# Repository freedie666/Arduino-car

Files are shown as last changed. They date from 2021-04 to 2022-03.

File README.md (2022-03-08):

# Arduino Car
  
Robotic car that follows line drawn on the ground using arduino.

Project was created at BUT-FIT
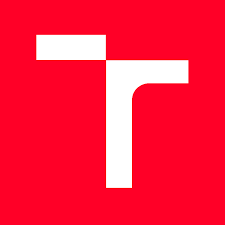
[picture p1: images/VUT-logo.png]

, class IMR.

<p align="center">
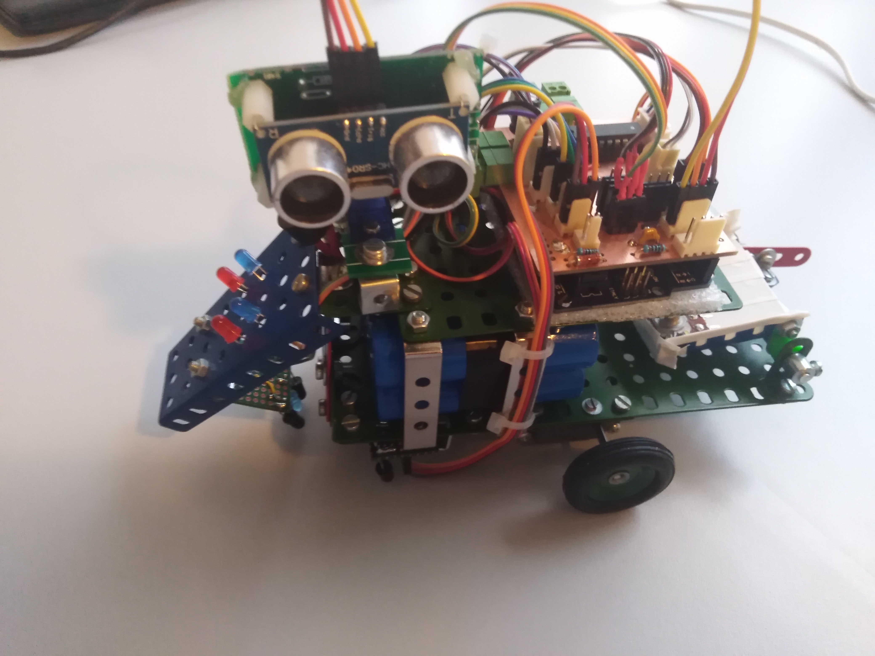
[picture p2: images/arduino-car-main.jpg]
  
</p>

## What robot does

> - Follows line at the ground
> - Can detect extra line that tells robot where to go at the crossroads
> - Extra lines can give robot additional orders
> - Detection of obstacle on the line
> - Robot can find best way around obstacle and avoid it
> - Is able to carry cargo and unload it on command
> - Sings a song when detects obstacle
> - Has multiple Blue and RED LEDs that show its intentions
> - Carries its own power source - batteries

## How its done

> - Brain of the operation is Arduino UNO
> - Car is powered by two 12V DC motors with gearbox
> - Motors are controlled by motor driver LV8406 using PWM
> - Lines are detected by infrared emiting LED and phototransistor [3x LED and 4x phototransistors]
> - Speed and directions are controlled by P-regulator
> - Obstacles are detected with ultrasonic sensor HC-SR04 
> - Ultrasonic sensor is mounted on small servo, providing range of detection up to +-90° 
> - Cargo beds movement is provided by stepper motor 2BYJ-48
> - Blue and RED LEDs are controlled by WS2818B led driver
> - Buzzer can play All star song which is stored in Flash memory

## Last notes

> - Everything electical is soldered at custom made PCB which fits onto Arduino as Arduino shield
> - Song is stacked in memory in a way to save as much memory as possible [4 numbers in one unsigned short]
  
## Links 
Demonstration of car at [Youtube](https://www.youtube.com/watch?v=gtERXzQzxGM)

More photos and videos at [Google Drive](https://drive.google.com/drive/folders/1pzaO6EnN3uHb_-Xj_Ckr5q-n50d8h_We?usp=sharing)

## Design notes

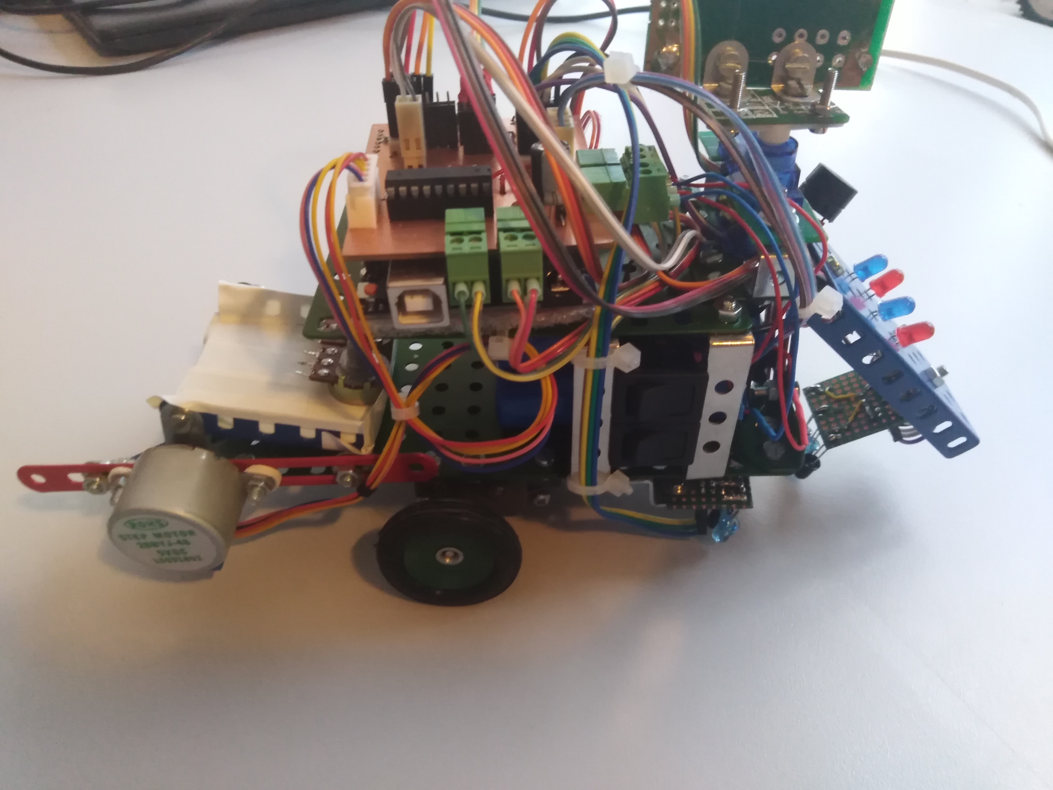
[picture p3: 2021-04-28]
images/arduino-car-main2.jpg

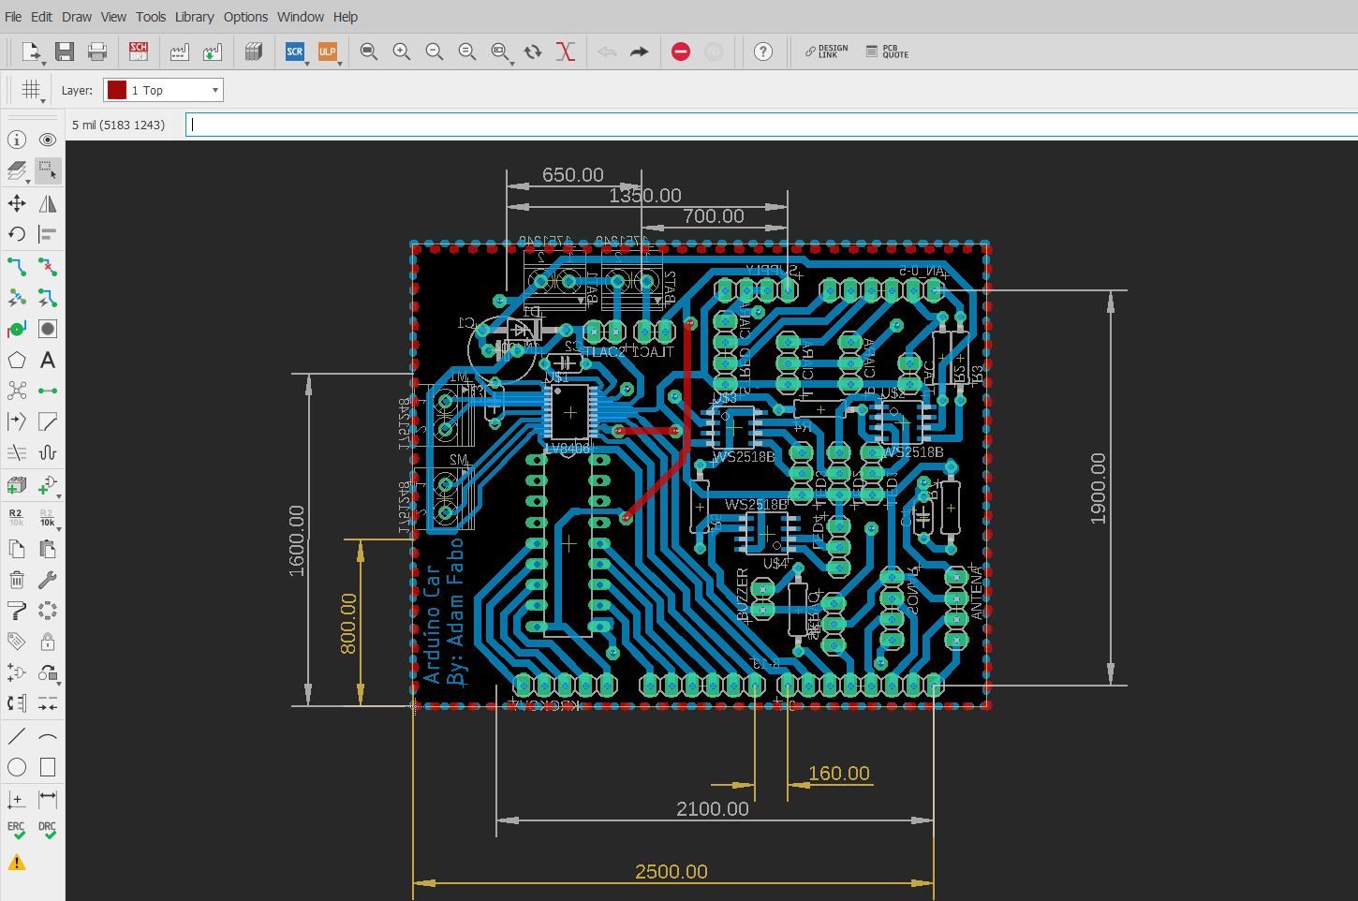
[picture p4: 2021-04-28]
PCB/PCB1.png

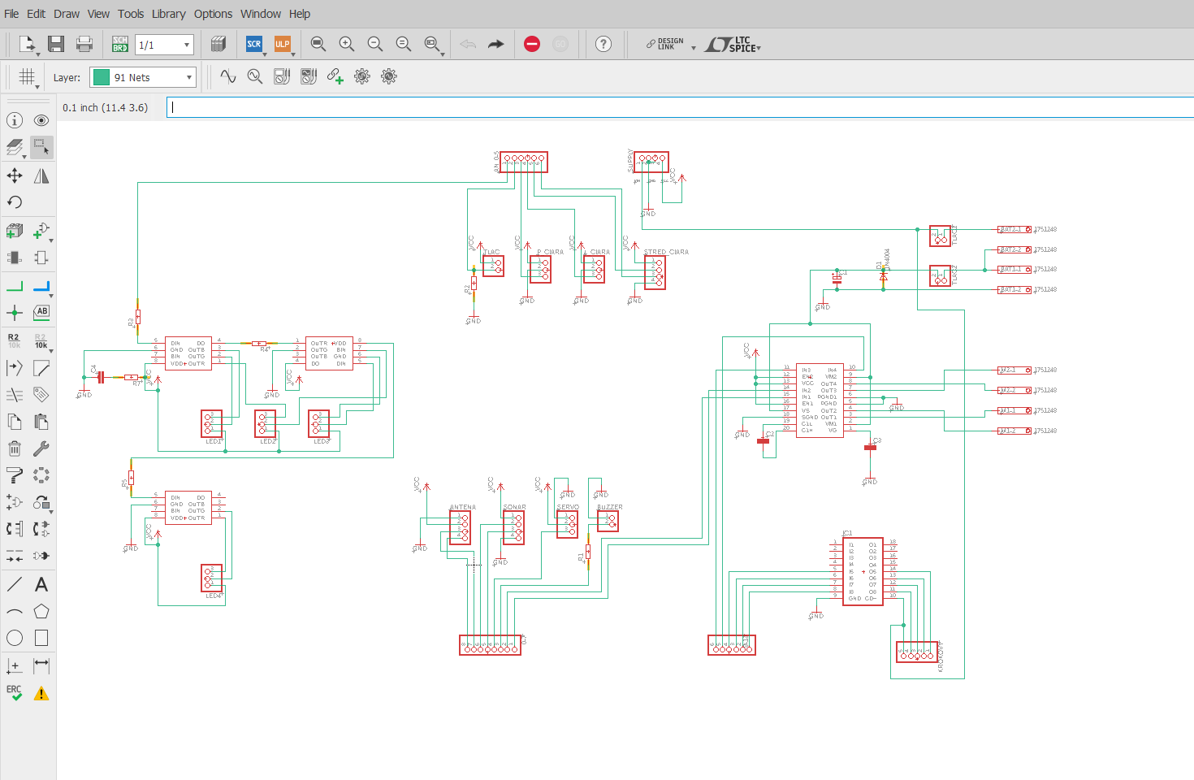
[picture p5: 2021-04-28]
PCB/PCB2.png

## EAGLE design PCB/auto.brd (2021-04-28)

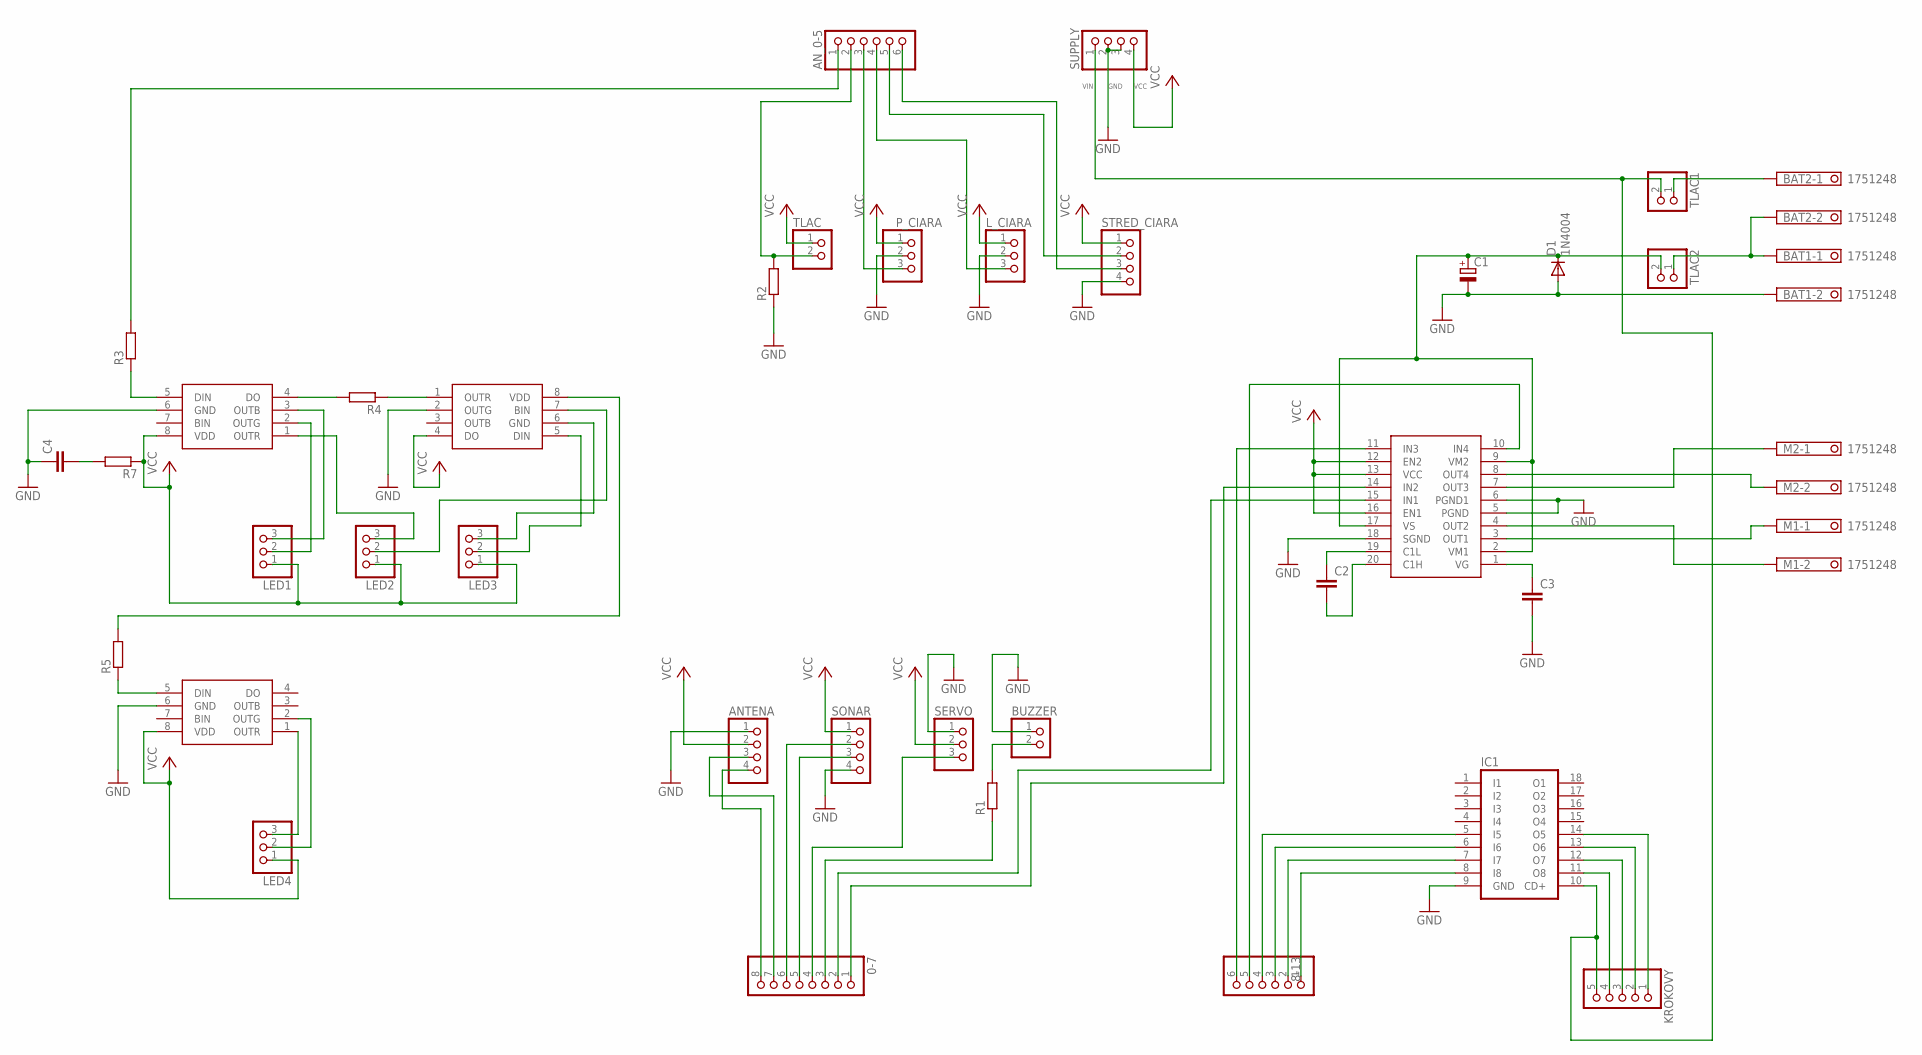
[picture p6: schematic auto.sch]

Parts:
0-7: PINHD-1X8; 1X08
8-13: PINHD-1X6; 1X06
ANTENA: PINHD-1X4; 1X04
AN_0-5: PINHD-1X6; 1X06
BAT1, BAT2: 1751248
BUZZER: PINHD-1X2; 1X02
C1: CPOL-EUE3.5-8; E3,5-8
C2, C3, C4: C-EU050-024X044; C050-024X044
D1: 1N4004; DO41-10
IC1: ULN2804A; DIL18
KROKOVY: PINHD-1X5; 1X05
LED1, LED2, LED3, LED4: PINHD-1X3; 1X03
L_CIARA: PINHD-1X3; 1X03
M1, M2: 1751248
P_CIARA: PINHD-1X3; 1X03
R1, R2, R3, R4, R5, R7: R0207/10; 0207/10
SERVO: PINHD-1X3; 1X03
SONAR: PINHD-1X4; 1X04
STRED_CIARA: PINHD-1X4; 1X04
SUPPLY: PINHD-1X4; 1X04
TLAC, TLAC1, TLAC2: PINHD-1X2; 1X02
U$1: LV8406; TSSOP20
U$2, U$3, U$4: WS2518B; SOP08

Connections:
GND: ANTENA.1, BAT1.2, BUZZER.1, C1.-, C3.2, C4.1, D1.A, IC1.9 (GND), L_CIARA.2, P_CIARA.2, R2.1, SERVO.1, SONAR.4, STRED_CIARA.4, SUPPLY.2, SUPPLY.3, U$1.5 (PGND), U$1.6 (PGND1), U$1.18 (SGND), U$2.6 (GND), U$3.2 (OUTG), U$4.6 (GND)
unnamed: AN_0-5.6, STRED_CIARA.3
unnamed: AN_0-5.5, STRED_CIARA.2
unnamed: AN_0-5.4, L_CIARA.3
unnamed: AN_0-5.3, P_CIARA.3
unnamed: 0-7.6, SONAR.2
unnamed: 0-7.5, SONAR.3
unnamed: 0-7.4, SERVO.3
unnamed: C3.1, U$1.1 (VG)
unnamed: BAT1.1, BAT2.2, TLAC2.1
unnamed: BUZZER.2, R1.2
unnamed: 0-7.3, R1.1
unnamed: BAT2.1, TLAC1.1
unnamed: 8-13.4, IC1.5 (I5)
unnamed: 8-13.3, IC1.6 (I6)
unnamed: 8-13.2, IC1.7 (I7)
unnamed: 8-13.1, IC1.8 (I8)
unnamed: M1.1, U$1.3 (OUT1)
unnamed: IC1.11 (O8), KROKOVY.4
unnamed: IC1.12 (O7), KROKOVY.3
unnamed: IC1.14 (O5), KROKOVY.1
unnamed: IC1.13 (O6), KROKOVY.2
unnamed: M1.2, U$1.4 (OUT2)
unnamed: M2.1, U$1.7 (OUT3)
unnamed: M2.2, U$1.8 (OUT4)
unnamed: C1.+, D1.C, TLAC2.2, U$1.2 (VM1), U$1.9 (VM2), U$1.17 (VS)
unnamed: 8-13.5, U$1.10 (IN4)
unnamed: 8-13.6, U$1.11 (IN3)
unnamed: C2.1, U$1.19 (C1L)
unnamed: C2.2, U$1.20 (C1H)
unnamed: R5.1, U$4.5 (DIN)
unnamed: LED4.3, U$4.1 (OUTR)
unnamed: 0-7.1, U$1.14 (IN2)
unnamed: R5.2, U$3.8 (VDD)
unnamed: AN_0-5.1, R3.2
unnamed: LED2.2, U$3.7 (BIN)
unnamed: LED1.3, U$2.3 (OUTB)
unnamed: LED4.2, U$4.2 (OUTG)
unnamed: R4.1, U$3.1 (OUTR)
unnamed: R3.1, U$2.5 (DIN)
unnamed: LED3.3, U$3.6 (GND)
unnamed: LED3.2, U$3.5 (DIN)
unnamed: AN_0-5.2, R2.2, TLAC.2
unnamed: 0-7.2, U$1.15 (IN1)
unnamed: LED1.2, U$2.2 (OUTG)
unnamed: 0-7.7, ANTENA.3
unnamed: 0-7.8, ANTENA.4
unnamed: R4.2, U$2.4 (DO)
unnamed: LED2.3, U$2.1 (OUTR)
unnamed: C4.2, R7.2
VCC: ANTENA.2, LED1.1, LED2.1, LED3.1, LED4.1, L_CIARA.1, P_CIARA.1, R7.1, SERVO.2, SONAR.1, STRED_CIARA.1, SUPPLY.4, TLAC.1, U$1.12 (EN2), U$1.13 (VCC), U$1.16 (EN1), U$2.8 (VDD), U$3.4 (DO), U$4.8 (VDD)
VIN: IC1.10 (CD+), KROKOVY.5, SUPPLY.1, TLAC1.2

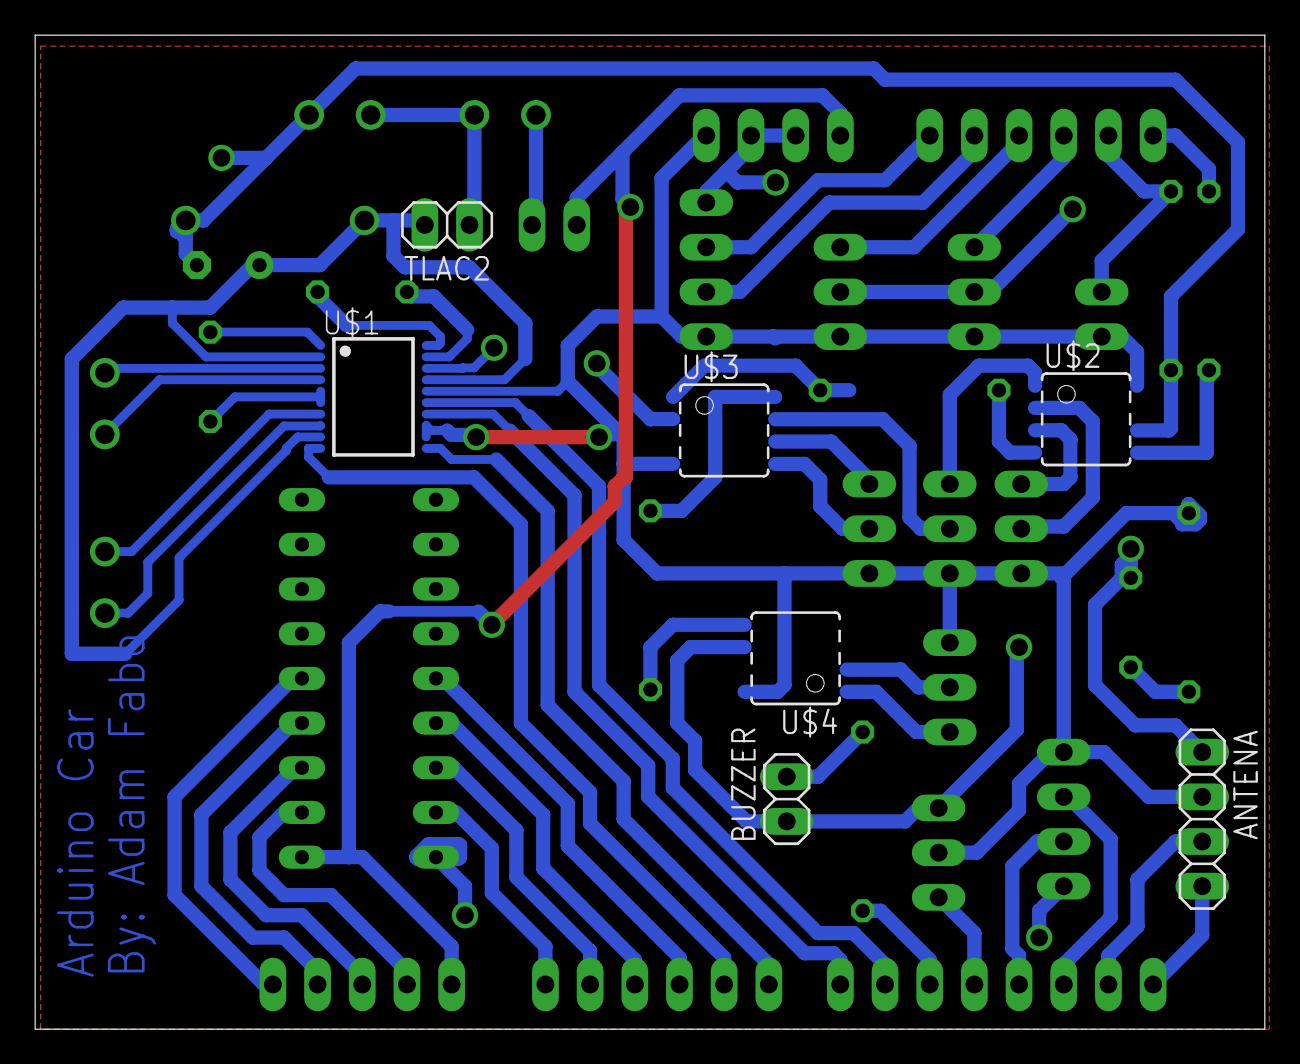
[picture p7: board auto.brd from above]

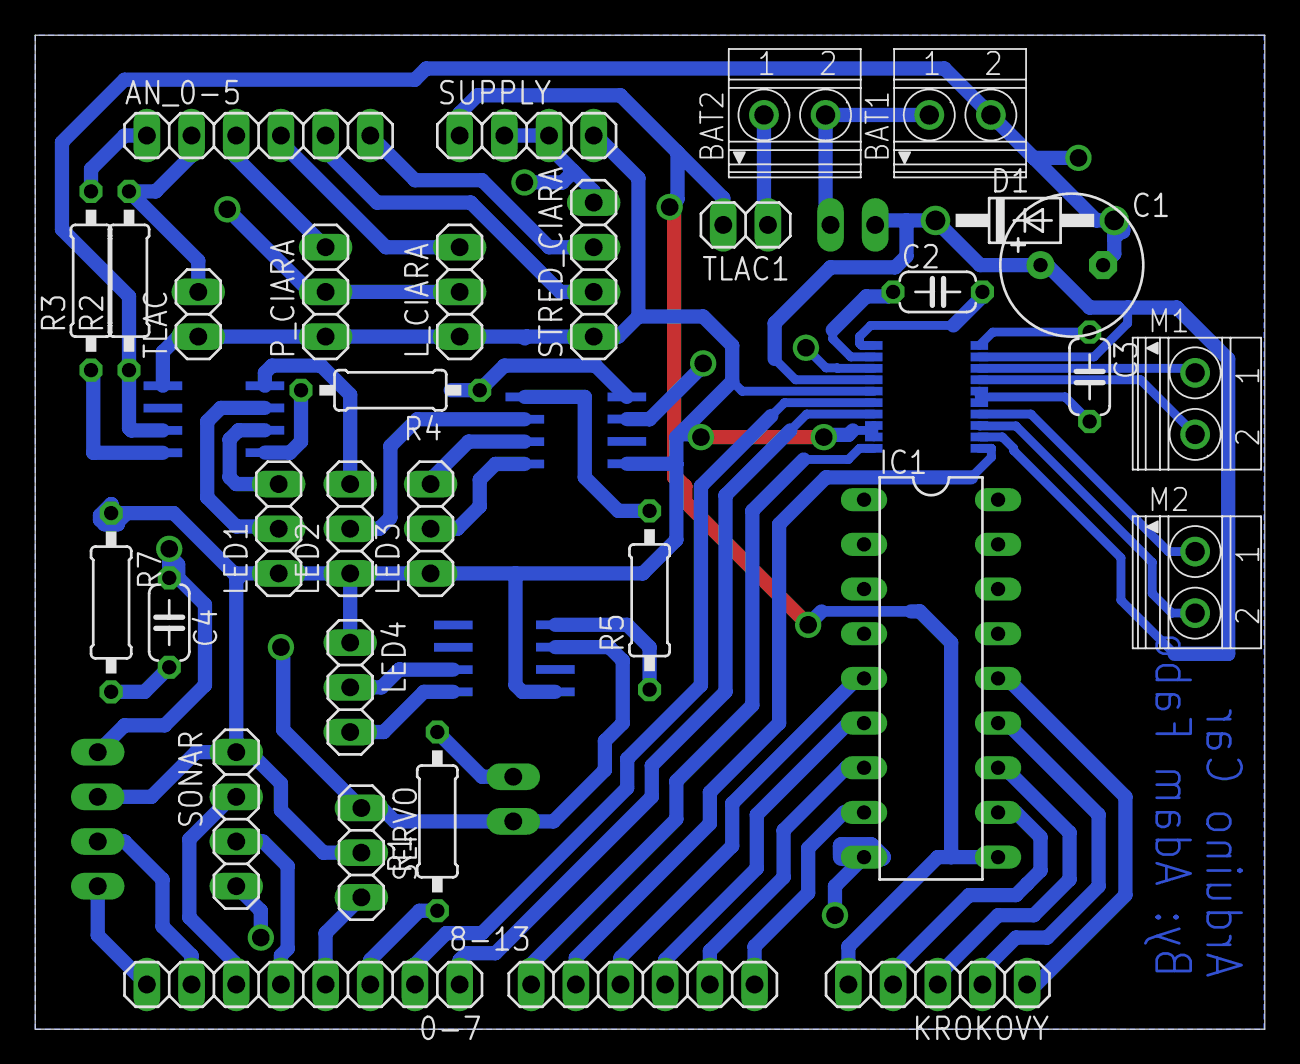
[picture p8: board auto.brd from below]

Board: 2 copper layers, 69.9 x 56.5 mm, 39 parts (32 on the bottom side), 52 nets.

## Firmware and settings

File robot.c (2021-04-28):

// Proejkt na predmet IMR
// Autor: Adam Fabo
// Subor obsahuje kod pre ovladanie pohybu robota po ciernej ciare 

#include <Servo.h>
// 3 lavy

// data pre all-star melodiu
const short PROGMEM tones[]   =  {370, 554, 466, 466, 415, 370, 370, 494, 466, 466, 415, 415, 370, 370, 554, 466, 466, 415, 370, 370, 311, 277, 370, 370, 554, 466, 466, 415, 415, 369, 369, 494, 466, 466, 415, 415, 369, 369, 554, 466, 466, 415, 369, 369, 415, 311, 369, 311, 369, 369, 369, 369, 311, 277, 369, 369, 369, 369, 369, 369, 369, 369, 369, 369, 369, 369, 369, 466, 369, 466, 466, 554, 494, 466, 369, 415, 415, 415, 415, 466, 369, 369, 311, 277, 369, 369, 369, 466, 554, 466, 622, 466, 554, 466, 622, 466, 554, 494, 466, 415, 369, 369, 415, 369, 369, 369, 369, 369, 369, 369, 369, 369, 369, 369, 466, 369, 369, 369, 311, 311};
const unsigned short dels[] PROGMEM  = {16932, 16930, 8738, 8740, 8740, 8804, 8738, 16930, 8738, 9250, 8770, 4964, 4386, 8721, 4625, 4385, 4625, 8467, 8466, 8498, 4386, 4642, 4626, 4626, 8738, 16914, 8465, 16913, 4369, 8466};

Servo myservo;

// sonar
#define ECHO_PIN 3
#define TRIG_PIN 2

//buzzer
#define PIEZO_PIN 4
#define TONES_LEN 120

//servo
#define SERVO_PIN 5

//motor
#define MOTOR_L1 6
#define MOTOR_L2 7
#define MOTOR_R1 8
#define MOTOR_R2 9

//krokovy motor
#define STEPPER_1 10
#define STEPPER_2 11
#define STEPPER_3 12
#define STEPPER_4 13

//pocet krokov potrebnych na zodvihnutie korby
#define STEPPER_STEPS 150

//led driver
#define LED_PIN 19

// flagy pre nastavovanie lediek
#define NONE  B00000000
#define RBLUE B00000001
#define LBLUE B00000010
#define LRED  B00000100
#define RRED  B00001000



#define DIST_target 15.0
#define DIST_target_wall 22.0
#define DIST_koef_add 9
#define DIST_koef_sub 3


#define target  700       // Koeficienty P regulatora pre snimanie stredu ciary
#define P_koef_add  0.7
#define P_koef_sub  1.5


#define target_low 200   // Koeficienty P regulatora pre snimanie hrany ciary
#define target_high 700
#define P_koef_add_hrana  0.2
#define P_koef_sub_hrana  0.5

#define hysteresis_up 650
#define hysteresis_down 450

#define koef 2

unsigned int min_speed     = 300 * koef;    // toto teoreticky cez define
unsigned int max_speed_add = 40  * koef;
unsigned int max_speed_sub = 20  * koef;

unsigned int periode = 1000 * koef;         // toto teoreticky cez define

unsigned int avgR = 500;
unsigned int avgL = 500;

unsigned long int smerovka_vpravo = 0;
unsigned long int smerovka_vlavo  = 0;

enum Mode { MODE_STRAIGHT, MODE_LEFT, MODE_RIGHT, MODE_GIVEN_RIGHT, MODE_GIVEN_LEFT,  MODE_KORBA};
Mode mode = MODE_STRAIGHT;
Mode mode_old = -1;// na zaciatok nejaku nevalidnu hodnotu

Mode modes_arr[] = {MODE_GIVEN_LEFT,MODE_KORBA};
int modes_counter = 0;

unsigned int filter_up = 18;              // toto teoreticky cez define
unsigned int filter_down = 40;            // toto teoreticky cez define


unsigned int counter = 6;                 // toto teoreticky cez define

unsigned int cnt = 0;

long duration;
float distance;

unsigned int delR = min_speed;
unsigned int delL = min_speed;

unsigned int num_of_cycles = 250;

unsigned int range_slow = 0;
bool once  = true;


unsigned int not_ciara_koef = 50 * koef;


int x = 20000;
bool can_go = true;
int pos = 0;
#define treshold  800;



void setup() {
  pinMode(TRIG_PIN, OUTPUT);     // sonar
  pinMode(ECHO_PIN, INPUT);

  pinMode(PIEZO_PIN, OUTPUT);

  pinMode(MOTOR_L1, OUTPUT);    // motor
  pinMode(MOTOR_L2, OUTPUT);
  pinMode(MOTOR_R1, OUTPUT);
  pinMode(MOTOR_R2, OUTPUT);

  pinMode(STEPPER_1, OUTPUT);   // krokovy
  pinMode(STEPPER_2, OUTPUT);
  pinMode(STEPPER_3, OUTPUT);
  pinMode(STEPPER_4, OUTPUT);

  digitalWrite(STEPPER_1, LOW);
  digitalWrite(STEPPER_2, LOW);
  digitalWrite(STEPPER_3, LOW);
  digitalWrite(STEPPER_4, LOW);

  myservo.attach(SERVO_PIN);
  Serial.begin(230400);
  Serial.println("Lets start this bitch");

  pinMode(LED_PIN, OUTPUT);
  digitalWrite(LED_PIN, LOW);
}


// hlavna smycka programu
void loop() {

  // stara sa o detekciu prekazok, ak na nejaku narazi tak prebera vedenie robota a postara sa o obidenie prekazky
  // ak ziadnu prekazku nedetekoval tak konci
  // ak detekoval potencialnu prekazku tak nastavuje hodnotu range_slow ktora spomali auto az dokedy bud nedetekuje prekazku uplne
  // alebo prekazka zmizne
  // taktiez nastavuje aj num_of_cycles - cim blizsie ku prekazke, tym menej cyklov
  obstacle_detection();


  main_func();

}

// hlavna funkcia robota
void main_func() {

  for (unsigned i = 0; i < num_of_cycles; i++) {
    // nastavenie serva dopredu
    myservo.write(80);

    // spomalenie robota ak je blizko prekazky
    delR -= min(range_slow, delR);
    delL -= min(range_slow, delL);

    motor_forward_PWM();



    // hodoty hlavneho snimaca ciary
    avgR = analogRead(1);
    avgL = analogRead(0);


    // branie kazdej n-tej hodnoty na spomalenie rastu hodnoti s kombinacou filtra
    // ak napr auto krizuje inu ciaru tak aby to nebralo ako falosnu detekciu smerovacej ciary
    if (i % counter == 0) {
      smerovka_vpravo = (filter_down * smerovka_vpravo + analogRead(2)) / (filter_down + 1) ;
      smerovka_vlavo  = (filter_down * smerovka_vlavo  + analogRead(3)) / (filter_down + 1) ;
    }

    /*Serial.print("\t");

      Serial.print(" smerovka_vpravo:  ");
      Serial.print(smerovka_vpravo);
      Serial.print("\t");
      Serial.print(" smerovka_vlavo:  ");
      Serial.println(smerovka_vlavo);*/


    if (mode == MODE_RIGHT || mode == MODE_GIVEN_RIGHT) {

      // Drzanie sa pravej hrany pasky

      if (mode != mode_old ) {
        Serial.println("MODE_RIGHT");
        Serial.println(mode);
        mode_old = mode;
        if (mode == MODE_RIGHT)
          shine_LED(RRED);
        else
          shine_LED(RBLUE | RRED);
      }


      //cast hysterezy
      if (mode == MODE_RIGHT && smerovka_vpravo < hysteresis_down ) {
        mode = MODE_STRAIGHT;
      } else if (mode == MODE_GIVEN_RIGHT && smerovka_vpravo < hysteresis_down && smerovka_vlavo < hysteresis_down) {
        mode = MODE_STRAIGHT;
      }

      calc_speed_right();

    } else if (mode == MODE_LEFT || mode == MODE_GIVEN_LEFT) {

      // Drzanie sa lavej hrany pasky

      if (mode != mode_old ) {
        Serial.println("MODE_LEFT");
        Serial.println(mode);
        mode_old = mode;
        if (mode == MODE_LEFT) {
          shine_LED( LRED);
        } else {
          shine_LED(LBLUE | LRED);
        }

      }
      //Serial.print("Dolava ");

      //cast hysterezy
      if (mode == MODE_LEFT && smerovka_vlavo < hysteresis_down ) {
        mode = MODE_STRAIGHT;
      } else if (mode == MODE_GIVEN_LEFT && smerovka_vpravo < hysteresis_down && smerovka_vlavo < hysteresis_down) {
        mode = MODE_STRAIGHT;
      }

      calc_speed_left();



    } else if (mode == MODE_STRAIGHT) {

      if (mode != mode_old ) {
        Serial.println("MODE_STRAIGHT");
        Serial.println(mode);
        mode_old = mode;
        shine_LED(LBLUE | RBLUE);
      }

      //Serial.print("No smer ");

      if (smerovka_vpravo > hysteresis_up && smerovka_vlavo < hysteresis_down) {
        mode  = MODE_RIGHT;

      } else if (smerovka_vlavo > hysteresis_up && smerovka_vpravo < hysteresis_down) {
        mode = MODE_LEFT;

      } else if (smerovka_vpravo > hysteresis_up && smerovka_vlavo > hysteresis_down) {

        mode = modes_arr[modes_counter % 2];
        modes_counter++;
        if(mode == MODE_KORBA){
          stepper_seq();
          mode = MODE_GIVEN_LEFT;
        }
          
      }

      calc_speed_straight();
    }

    delR = min(delR, periode);
    delL = min(delL, periode);
    Serial.print("  ");
    Serial.print(range_slow);
    Serial.print("  ");


    if (delR > delL) {
      Serial.print(" dolava \t");
    } else if (delR < delL) {
      Serial.print(" doprava \t");
    } else {
      Serial.print(" rovno \t");
    }

    Serial.print("\t");
    Serial.print(avgR);
    Serial.print(" R");
    Serial.print("\t");
    Serial.print(avgL);
    Serial.print(" L");


    Serial.print("\t");
    Serial.print(delR);
    Serial.print(" delR");
    Serial.print("\t");
    Serial.print(delL);
    Serial.println(" delL");


  }
}





void calc_speed_right() {
  if (avgL >= target_high && avgR <= target_low) { //chod rovno
    delR = min_speed;
    delL = min_speed;

  } else if (avgL <= target_high && avgL >= target_low && avgR <= target_low) { //ak je mimo kraja, viacej vlavo
    delL = min_speed - min(P_koef_sub_hrana * (target_high - avgL), min_speed);
    delR = min_speed + P_koef_add_hrana * (target_high - avgL);

  } else if (avgL >= target_high && avgR >= target_low) {                       //ak je trosku mimo stredu, viacej vpravo
    delL = min_speed + P_koef_add_hrana * (avgR - target_low);
    delR = min_speed - min(P_koef_sub_hrana * (avgR - target_low), min_speed);

  } else if (avgL <= target_low && avgR <= target_low) {    //ak je mimo ciary pokracuj v predoslom smere
    ;
    //delR = 0;
    //delL = 0;
  }
}


void calc_speed_left() {

  if (avgR >= target_high  &&  avgL <= target_low) { //chod rovno
    delR = min_speed;
    delL = min_speed;

  } else if (avgR <= target_high && avgR >= target_low && avgL <= target_low) { //ak je mimo kraja, viacej vlavo
    delR = min_speed - min(P_koef_sub_hrana * (target_high - avgR), min_speed);
    delL = min_speed + P_koef_add_hrana * (target_high - avgR);

  } else if (avgR >= target_high && avgL >= target_low) {                     //ak je trosku mimo stredu, viacej vpravo
    delR = min_speed + P_koef_add_hrana * (avgL - target_low);
    delL = min_speed - min(P_koef_sub_hrana * (avgL - target_low), min_speed);


  } else if (avgL <= target_low && avgR <= target_low) {                    //ak je mimo ciary pokracuj v predoslom smere
    ;//delR = 0;
    Serial.print(" POKRACUJEM  ");
    //delL = 0;
  }
}

void calc_speed_straight() {
  if (avgR >= target && avgL >= target) {                               //chod rovno
    delR = min_speed;
    delL = min_speed;

  } else if (avgR >= target && avgL < target) {                            //ak je to trosku mimo stredu, viacej vlavo
    delR = min_speed - min(P_koef_sub * (target - avgL), min_speed);
    delL = min_speed + P_koef_add * (target - avgL);

  } else if (avgR < target && avgL >= target) {                           //ak je to trosku mimo stredu, viacej vpravo
    delR = min_speed + P_koef_add * (target - avgR);
    delL = min_speed -  min(P_koef_sub * (target - avgR), min_speed);

  } else if (avgR < target && avgL < target && avgR < 100 && avgL < 100) { //ak su obe mimo pokracuj v smere kam si siel
    ;//delR = 0;
    Serial.print(" POKRACUJEM  ");
    // delL = 0;

  } else if (avgR < target && avgL < target && avgR > avgL) {             //ak je to mimo vlavo
    delR = min_speed - min(P_koef_sub * (target - avgL), min_speed); //0
    delL = min_speed + P_koef_add * (target - avgL);

  } else if (avgR < target && avgL < target && avgR < avgL) {            //ak je to mimo vpravo
    delR = min_speed + P_koef_add * (target - avgR);
    delL = min_speed - min(P_koef_sub * (target - avgR), min_speed); //0
  }
}

// stara sa o detekciu prekazok, ak na nejaku narazi tak prebera vedenie robota a postara sa o obidenie prekazky
// ak ziadnu prekazku nedetekoval tak konci
// ak detekoval potencialnu prekazku tak nastavuje hodnotu range_slow ktora spomali auto az dokedy bud nedetekuje prekazku uplne
// alebo prekazka zmizne
// taktiez nastavuje aj num_of_cycles - cim blizsie ku prekazke, tym menej cyklov
void obstacle_detection() {


  sonar();

  if (distance > DIST_target &&  distance < DIST_target + 15) {
    // ak este nenarazil na prekazku ale prekazka je uz blizko

    num_of_cycles = max(250 - (DIST_target - distance) * 10, 100);
    range_slow    = min((DIST_target + 15 - distance  ) * 9, 80);
    

    Serial.print(num_of_cycles );
    Serial.print(" " );
    Serial.print(range_slow );
    Serial.print(" " );
    Serial.print(distance);
    Serial.println(" cm");


  } else if (distance < DIST_target) {
    //ak uz narazil na prekazku

    delR = 0;
    delL = 0;

    stop_motor();

    obstacle_seq();
    range_slow = 0;
    return;

  } else {
    num_of_cycles = 500 ;
    range_slow    = 0;
  }
}

// sekvencia ktora sa vykona ak robot natrafi na prekazku
void obstacle_seq() {
  // na zaciatku nejake zapiskanie
  //sing_a_song();
  delay(5000);

  // nasnimanie vzdialenosti
  int dst = 15;
  for (int i = 0; i < 10; i++) {
    sonar();

    //vyfiltrovanie vzdialenosti
    dst = (9 * dst + distance) / (9 + 1);
  }

  //ak tam uz prekazka nie je tak ide sa dalej
  if (dst > 15)
    return;

  //zistenie ci nahodou robot nestoju na pomocnych pasikoch ktore by udavali jeho nasledovny smer
  for (int i = 0 ; i < 20; i++) {
    //filter na spomalenie rastu hodnoty
    smerovka_vpravo = (9 * smerovka_vpravo + analogRead(2)) / (9 + 1) ;
    smerovka_vlavo  = (9 * smerovka_vlavo +  analogRead(3)) / (9 + 1) ;


    /*Serial.print("\t");
      Serial.print(smerovka_vpravo);
      Serial.print(" R");
      Serial.print("\t");
      Serial.print(smerovka_vlavo);
      Serial.println(" L");*/
  }

  int dstR = 0;
  int dstL = 0;


  if (smerovka_vlavo < 500 &&  smerovka_vpravo < 500) {
    // ak sa ani jeden pasik nenachadza tak sa robot rozhodne sam
    // podla toho na ktorej strane je vacsia volna vzdialenost tak tam pojde

    myservo.write(0);
    delay(1000);

    // ziskanie vzdialenosti doprava od robota
    for (int i = 0; i < 30; i++) {
      sonar();
      dstR = (9 * dstR + distance) / (9 + 1);
    }

    myservo.write(180);
    delay(1000);

    // ziskanie vzdialenosti dolava od robota
    for (int i = 0; i < 30; i++) {
      sonar();
      dstL = (9 * dstL + distance) / (9 + 1);
    }

    if (dstR < dstL) {
      rotate_left();

      myservo.write(0);
      delay(500);

      follow_right();

    } else {
      rotate_right();

      myservo.write(180);
      delay(500);

      follow_left();
    }


  } else if (smerovka_vlavo > 700 &&  smerovka_vpravo < 500) {
    // ak pomocny pasik je nalavo od robota

    rotate_left();

    myservo.write(0);
    delay(500);

    follow_right();

  } else if (smerovka_vlavo < 500 &&  smerovka_vpravo > 700) {
    // ak pomocny pasik je napravo od robota

    rotate_right();

    myservo.write(180);
    delay(500);

    follow_left();

  } else if ( (smerovka_vlavo > 500 &&  smerovka_vpravo > 700) || (smerovka_vlavo > 700 &&  smerovka_vpravo > 500) ) {
    ; // podla pamate

    rotate_right();

    myservo.write(180);
    delay(500);

    follow_left();
    
  }

}

// robot sa bude drzat steny co je nalavo od neho
void follow_left() {
  avgR = 0;
  avgL = 0;

  while (1) {
    myservo.write(170); // nastavenie serva dolava
    sonar();

    // orezanie maximalnej hodnoty ktoru moze sonar nasnimat
    // bez toho vdaka napr chybnej vzdialenosti alebo velkej hodnote by mohol robot zabludit
    distance = min(distance, 30);

    // P regulator na udrzanie si vzdialenosti od steny
    if (distance < DIST_target_wall) {
      delR = min_speed - min(DIST_koef_add * (abs(distance - DIST_target_wall)) + not_ciara_koef, min_speed);
      delL = min_speed + min(DIST_koef_sub * (abs(distance - DIST_target_wall)) + not_ciara_koef, min_speed);

    } else {
      delR = min_speed + min(DIST_koef_sub * (abs(distance - DIST_target_wall)) + not_ciara_koef, min_speed);
      delL = min_speed - min(DIST_koef_add * (abs(distance - DIST_target_wall)) + not_ciara_koef, min_speed);

    }

    for (int i = 0; i < 25; i++) {
      // snimanie honot z hlavneho snimaca,
      // na hodnoty je pouzity filter na spomalenie rastu hodnoty
      avgR = (9 * avgR + analogRead(1)) / (9 + 1) ;
      avgL = (9 * avgL + analogRead(0)) / (9 + 1) ;

      // ak narazil na ciaru tak sa nastavi zatocenie doprava a funkcia sa konci
      if (avgR > 700 || avgL > 700) {
        delR = 0;
        delL = 750;

        for (int j = 0; j < 100; j++) {
          Serial.println(" tuna sooooooooooooom");
          motor_forward_PWM();
        }

        return;
      }

      motor_forward_PWM();
    }
  }
}


// robot sa bude drzat steny co je napravo od neho
void follow_right() {
  avgR = 0;
  avgL = 0;

  while (1) {
    myservo.write(0);   // nastavenie serva doprava
    sonar();

    // orezanie maximalnej hodnoty ktoru moze sonar nasnimat
    // bez toho vdaka napr chybnej vzdialenosti alebo velkej hodnote by mohol robot zabludit
    distance = min(distance, 30);

    // P regulator na udrzanie si vzdialenosti od steny
    if (distance < DIST_target_wall) {
      delR = min_speed + min(DIST_koef_add * (abs(distance - DIST_target_wall)) + not_ciara_koef, min_speed);
      delL = min_speed - min(DIST_koef_sub * (abs(distance - DIST_target_wall)) + not_ciara_koef, min_speed);

    } else {
      delR = min_speed - min(DIST_koef_sub * (abs(distance - DIST_target_wall)) + not_ciara_koef, min_speed);
      delL = min_speed + min(DIST_koef_add * (abs(distance - DIST_target_wall)) + not_ciara_koef, min_speed);

    }

    for (int i = 0; i < 25; i++) {
      // snimanie honot z hlavneho snimaca,
      // na hodnoty je pouzity filter na spomalenie rastu hodnoty
      avgR = (9 * avgR + analogRead(1)) / (9 + 1) ;
      avgL = (9 * avgL + analogRead(0)) / (9 + 1) ;

      // ak narazil na ciaru tak sa nastavi zatocenie doprava a funkcia sa konci
      if (avgR > 700 || avgL > 700) {
        delR = 750;
        delL = 0;

        for (int j = 0; j < 100; j++)
          motor_forward_PWM();

        return;
      }

      motor_forward_PWM();
    }
  }
}

// otoci robota dolaba o zhruba 90 deg
// funkcia nema ziadnu spatnu vazbu takze zalezi iba od poctu cyklov
void rotate_left() {

  for (int i = 0; i < 550; i++) {

    digitalWrite(MOTOR_L1, HIGH);
    digitalWrite(MOTOR_R2, HIGH);


    digitalWrite(MOTOR_R1, LOW);
    digitalWrite(MOTOR_L2, LOW);

    int rotation_speed = 300 * koef;

    delayMicroseconds (rotation_speed);

    digitalWrite(MOTOR_R2, LOW);
    digitalWrite(MOTOR_L1, LOW);
    delayMicroseconds(periode - rotation_speed);
  }

  stop_motor();
}


// otoci robota doprava o zhruba 90 deg
// funkcia nema ziadnu spatnu vazbu takze zalezi iba od poctu cyklov
void rotate_right() {

  for (int i = 0; i < 550; i++) {
    digitalWrite(MOTOR_L1, LOW);
    digitalWrite(MOTOR_R2, LOW);


    digitalWrite(MOTOR_R1, HIGH);
    digitalWrite(MOTOR_L2, HIGH);

    int rotation_speed = 300 * koef;

    delayMicroseconds (rotation_speed);

    digitalWrite(MOTOR_R1, LOW);
    digitalWrite(MOTOR_L2, LOW);
    delayMicroseconds(periode - rotation_speed);
  }

  stop_motor();
}

// vytvori kratky brzdiaci impulz
void stop_motor() {

  digitalWrite(MOTOR_R1, HIGH);
  digitalWrite(MOTOR_L1, HIGH);

  digitalWrite(MOTOR_L2, HIGH);
  digitalWrite(MOTOR_R2, HIGH);
  delay(1);
}


// hlavna funkcia pre pohyb robota smerom vpred
// funkcia zoberie delR a delL a na kazdy motor pusti PWM ktoreho dlzka zodpoveda periode
// a za stav v jednotke zodpoveda velkost delR a delL
// pre kombinacie pohybu viz. https://www.onsemi.com/pdf/datasheet/lv8406t-d.pdf
void motor_forward_PWM() {

  digitalWrite(MOTOR_R1, LOW);    //nastavenie motorov
  digitalWrite(MOTOR_L1, LOW);

  if (delR == 0 && delL == 0) {
    digitalWrite(MOTOR_L2, LOW);
    digitalWrite(MOTOR_R2, LOW);
  } else {
    digitalWrite(MOTOR_L2, HIGH);
    digitalWrite(MOTOR_R2, HIGH);
  }


  if (delR > delL) {                //perioda pwm
    delayMicroseconds(delL);
    digitalWrite(MOTOR_L2, LOW);

    delayMicroseconds(delR - delL);

    digitalWrite(MOTOR_R2, LOW);
    delayMicroseconds(periode - delR);

  } else if (delR < delL) {
    delayMicroseconds(delR);
    digitalWrite(MOTOR_R2, LOW);

    delayMicroseconds(delL - delR);
    digitalWrite(MOTOR_L2, LOW);
    delayMicroseconds(periode - delL);

  } else {
    delayMicroseconds(delR);

    digitalWrite(MOTOR_L2, LOW);
    digitalWrite(MOTOR_R2, LOW);
    delayMicroseconds(periode - delR);
  }
}


// hlavna funkcia pre pohyb robota smerom vpred
// funkcia zoberie delR a delL a na kazdy motor pusti PWM ktoreho dlzka zodpoveda periode
// a za stav v jednotke zodpoveda velkost delR a delL
// pre kombinacie pohybu viz. https://www.onsemi.com/pdf/datasheet/lv8406t-d.pdf
void motor_backward_PWM() {

  digitalWrite(MOTOR_R2, LOW);    //nastavenie motorov
  digitalWrite(MOTOR_L2, LOW);

  if (delR == 0 && delL == 0) {
    digitalWrite(MOTOR_L1, LOW);
    digitalWrite(MOTOR_R1, LOW);
  } else {
    digitalWrite(MOTOR_L1, HIGH);
    digitalWrite(MOTOR_R1, HIGH);
  }


  if (delR > delL) {                //perioda pwm
    delayMicroseconds(delL);
    digitalWrite(MOTOR_L1, LOW);

    delayMicroseconds(delR - delL);

    digitalWrite(MOTOR_R1, LOW);
    delayMicroseconds(periode - delR);

  } else if (delR < delL) {
    delayMicroseconds(delR);
    digitalWrite(MOTOR_R1, LOW);

    delayMicroseconds(delL - delR);
    digitalWrite(MOTOR_L1, LOW);
    delayMicroseconds(periode - delL);

  } else {
    delayMicroseconds(delR);

    digitalWrite(MOTOR_L1, LOW);
    digitalWrite(MOTOR_R1, LOW);
    delayMicroseconds(periode - delR);
  }
}

void sing_a_song() {

  // short na arduine ma 16 bitov
  // delay-e v pesnicke su nasobky 150 ms takze ak predelime delay-e 150 dostaneme cisla z intervalu 0-15 a to sa zmesti na 4 bity
  // tym padom sa daju do jedneho shoru zapisat 4 cisla ktore sa potom daju vybrat pomocou masky

  unsigned short d;
  unsigned short x = 15;
  for (int i = 0; i < TONES_LEN; i++) {
    d = (( pgm_read_word_near(dels + i / 4) & (x << ((i % 4) * 4)) ) >> ((i % 4) * 4)) * 150;
    tone(PIEZO_PIN, pgm_read_word_near(tones + i), d );
    delay(d);
  }


}
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
